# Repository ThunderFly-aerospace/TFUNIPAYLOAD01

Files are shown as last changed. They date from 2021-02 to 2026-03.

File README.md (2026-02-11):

# TFUNIPAYLOAD01 - universal interface for sensor payload 

Reference design of PX4 interface for generic [TF-ATMON](https://docs.thunderfly.cz/instruments/TF-ATMON) compatible payload. The purpose of this design is to connect a sensor to the [TF-ATMON](https://www.thunderfly.cz/tf-atmon.html) system, despite that the sensor does not have any driver in the flight stack (autopilot firmware), but at the same time, it is required for atmospheric measurement.

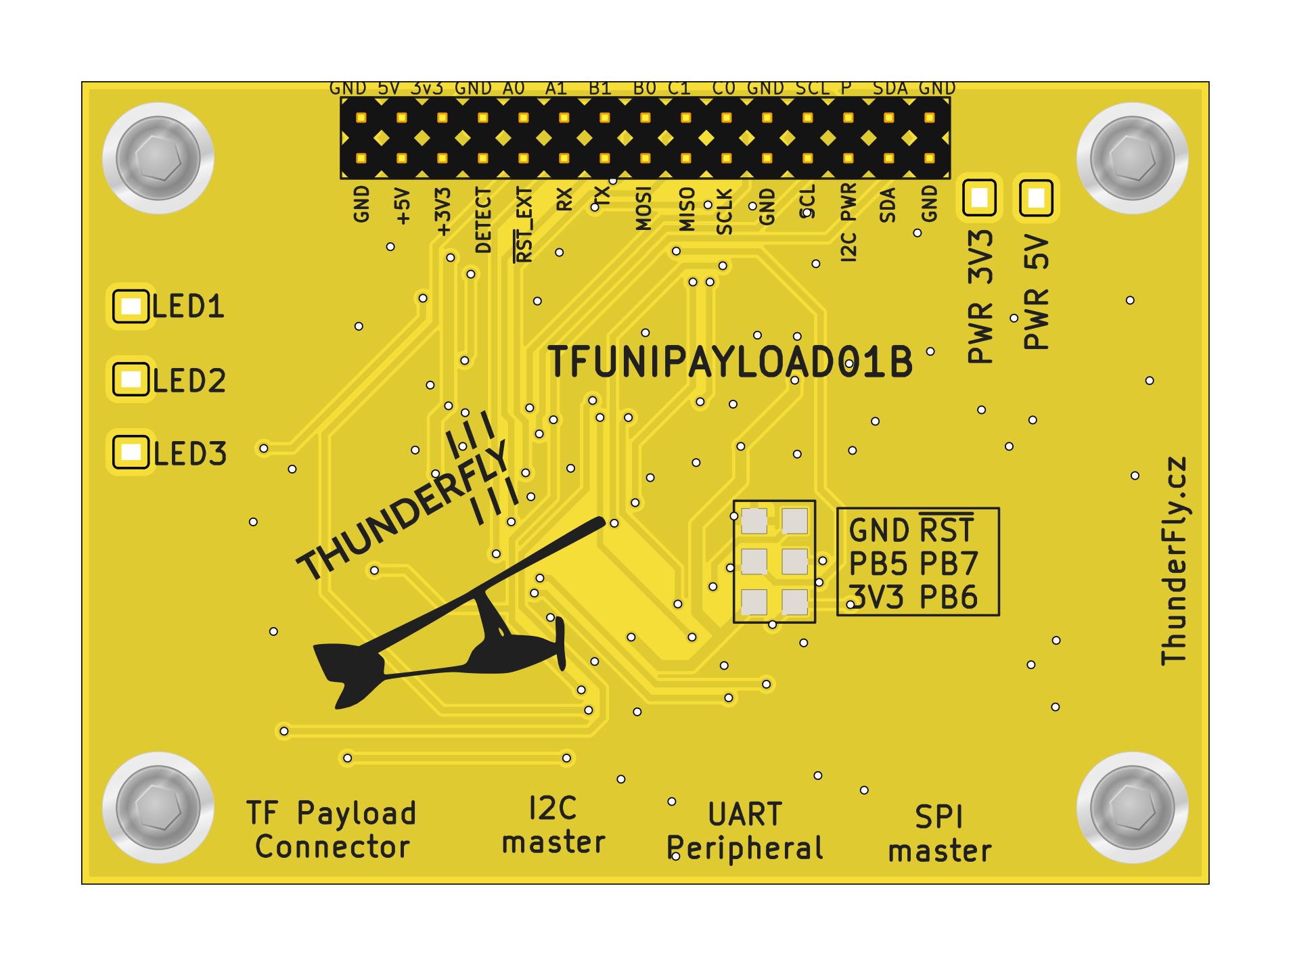
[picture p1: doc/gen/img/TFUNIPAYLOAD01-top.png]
TFUNIPAYLOAD top view


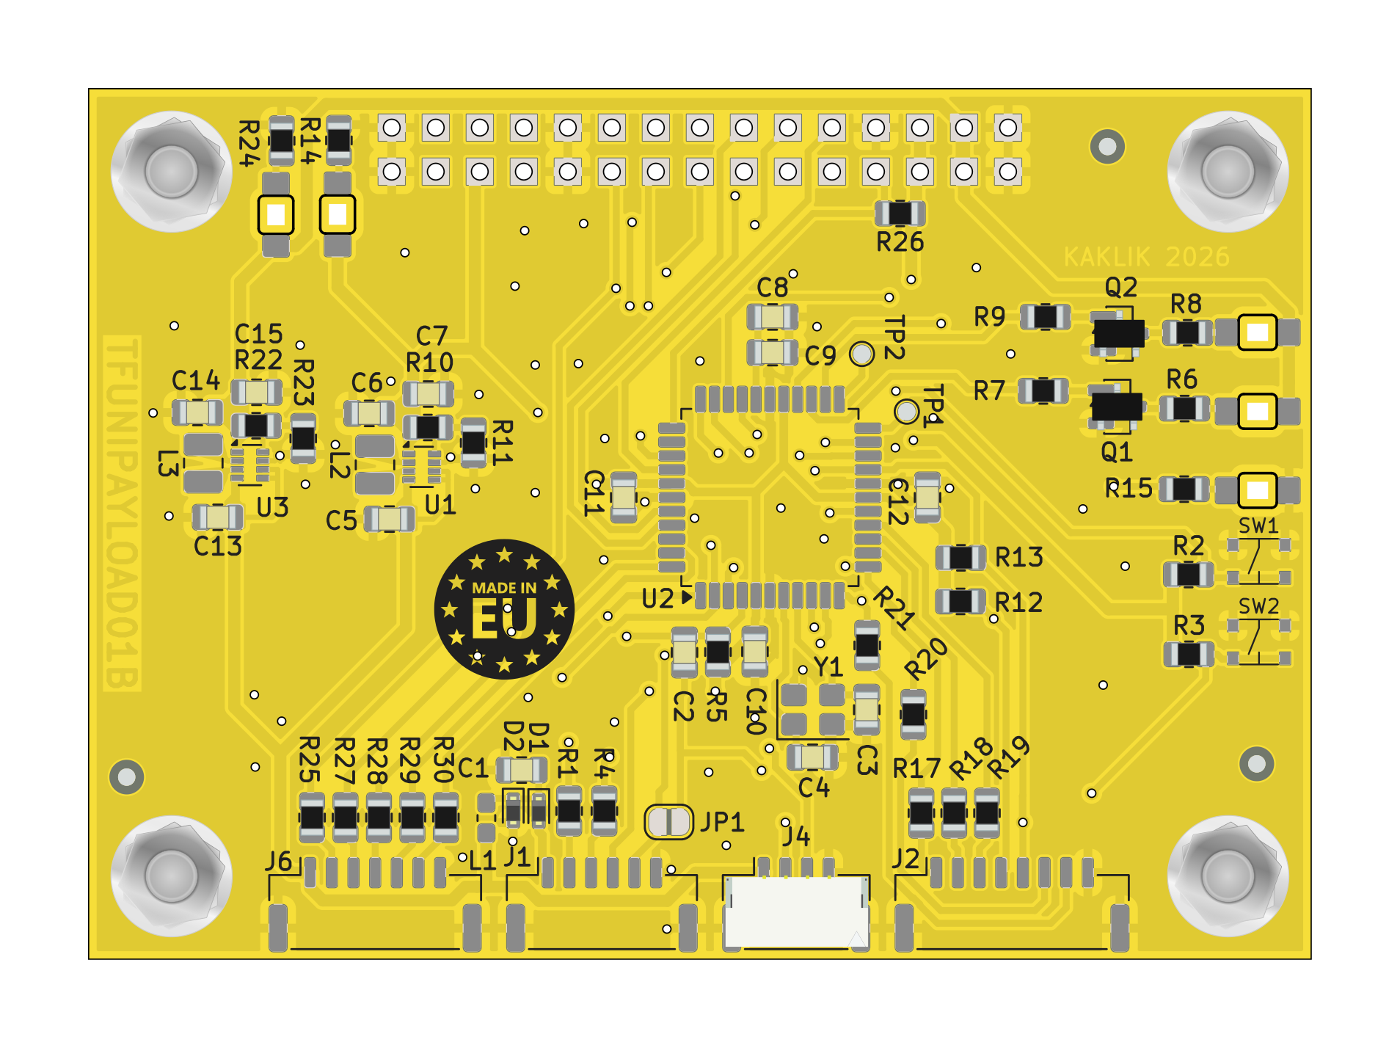
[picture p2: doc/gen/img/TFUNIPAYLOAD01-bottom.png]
TFUNIPAYLOAD01 bottom view


The sensor is connected to the TFUNIPAYLOAD board using a UART, I2C, GPIO, ADC, or SPI interface. 
ATmega in TFUNIPAYLOAD01 runs the Arduino firmware, which prepares [MAVLink](https://en.wikipedia.org/wiki/MAVLink) messages to be logged and transported to GCS running TF-ATMON infrastructure described in the block schematics. 

TFUNIPAYLOAD block-schematics

## Example of use

FMU firmware (PX4 or Ardupilot, for example) is capable of logging MAVLink data from the UART (Telemetry Port).  Therefore, the “UART Peripheral” connector on TFUNIPAYLOAD01 is intended for connecting a UART-based FMU using the Pixhawk DS-009 telemetry pinout. Typical devices include flight controllers (autopilot) or companion computers.

[Pixhawk standard connector pinout](https://github.com/pixhawk/Pixhawk-Standards/blob/master/DS-009%20Pixhawk%20Connector%20Standard.pdf) is as follows:

| Pin | Signal | Voltage levels  | Read/Write | Write |
| --- |:---:| ---:|---|---|
| 1 (red) | Vcc | +5V | Optional | Optional |
| 2 (blk) | TX (OUT)  | +3.3 V | PX4 -> Payload | -- |
| 3 (blk) | RX (IN) | +3.3 V | Payload -> PX4 | Payload -> PX4 |
| 4 (blk) | CTS (IN)  | +3.3 V | -- | -- |
| 5 (blk) | RTS (OUT) | +3.3 V | -- | -- |
| 6 (blk) | GND | GND | GND | GND |

For data to be received by the PX4 autopilot, it must have a specific form. Explicitly, it needs to use a serial link with  [MAVLink v2](https://mavlink.io/en/) packets. In that case, the [Tunnel (#385)](https://mavlink.io/en/messages/common.html#TUNNEL) packets will be stored in the autopilot's log file and forwarded to the GCS. 
The [TFUSBSERIAL01](https://github.com/ThunderFly-aerospace/TFUSBSERIAL01) hardware could be used to easily check for correct wiring. 

The following library [c_library_v2](https://github.com/mavlink/c_library_v2), which is automatically generated from message definition files, could be used. 

## Firmware examples

There are multiple Arduino-based firmware examples for different use cases. 

#### TFUNIPAYLOAD

[TFUNIPAYLOAD.ino](/SW/arduino/src/TFUNIPAYLOAD/TFUNIPAYLOAD.ino) contains a basic example, which listens to MAVLink messages from the autopilot and sends tunnel packets with random data to the autopilot.

#### TFUNIPAYLOAD_MINIMAL

Since message parsing requires a lot of memory, we have prepared an example where only [HEARTBEAT](https://mavlink.io/en/messages/common.html#HEARTBEAT) and [TUNNEL](https://mavlink.io/en/messages/common.html#TUNNEL) messages are sent. This example does not require a connected TX (from autopilot), and it is, therefore, suitable for MCUs with less memory.

Source code: [TFUNIPAYLOAD_MINIMAL.ino](/SW/arduino/src/TFUNIPAYLOAD_MINIMAL/TFUNIPAYLOAD_MINIMAL.ino)

#### Tunnel packet sending function

[Tunnel packet sending function](https://github.com/ThunderFly-aerospace/TFUNIPAYLOAD/blob/79eee22fe32725179d1df2b6ca72e901e2be1834/SW/arduino/src/TFUNIPAYLOAD/TFUNIPAYLOAD.ino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) ```  mav.SendTunnelData(data, sizeof(data), 0, 1, 0); ``` is the main function that enables sending tunnel data to the autopilot. It takes the following as its arguments:
 * data in uint8_t [127] format
 * data length
 * data type (every type of logged data will have its ID - it serves for easy differentiation of different sensors
 * target sysid
 * target compid

If the data only needs to be logged, the target sysid and compid must match the autopilot’s address, which is usually `sysid: 1, compid: 1`. If the data has to be logged and sent to GCS, broadcast must be set: `sysid: 1, compid: 0` or better `sysid: 0, compid: 0`. 

The autopilot only has a limited amount of storage memory (SD card), and it is therefore necessary to ensure, on the payload’s side, that it does not fill up during the flight. Alternatively, a maximum bandwidth on the MAVLink interface can be set in the autopilot. It is not tested what happens when the level set is exceeded[2021/09]. 

## Autopilot configuration

In the autopilot’s PX4 firmware, it is necessary to correctly set the following parameters (MAV_1_FORWARD and others will be visible only after setting the parameter MAV_1_CONFIG and rebooting the PX4): 

| Parametr | Value | Description |
|---|---|---|
| [MAV_1_CONFIG](http://docs.px4.io/main/en/advanced_config/parameter_reference.html#mavlink) | TELEM 2 | The port on which MAVLink packets will be expected. Any free TELEM port can be set |
| [MAV_1_FORWARD](http://docs.px4.io/main/en/advanced_config/parameter_reference.html#mavlink) | **1** | Enable message forwarding from this port|
| [MAV_1_RADIO_CTL](http://docs.px4.io/main/en/advanced_config/parameter_reference.html#mavlink) | **0** | |
| [MAV_1_RATE](http://docs.px4.io/main/en/advanced_config/parameter_reference.html#mavlink) | **0 B/s** | |
| [SER_TEL2_BAUD](http://docs.px4.io/main/en/advanced_config/parameter_reference.html#serial) | 57600 | It is necessary to configure the port that is set in `MAV_1_CONFIG` parameter. The setting of the baud rate port. |

How to set the parameters in PX4 is described in [manual](http://docs.px4.io/master/en/advanced_config/parameters.html#changing-a-parameter).

## How to check that the autopilot correctly receives MAVLink messages?

There are several options to find out whether the message sending is working correctly.

### Using the QGC

The message can be easily viewed live in [QGC](https://github.com/mavlink/qgroundcontrol/releases). For this procedure to function, two conditions must be fulfilled.

 1. The message must be broadcast, meaning the message must have set its target sysid and compid to 0, 0.
 2. The computer must be connected via a MAVLink instance that supports message forwarding (e.g., via TELEM1 port using modem or UART-USB converter); autopilot's USB does not support it.

 > Warning: this procedure will not work if the autopilot is connected via a USB cable to the Pixhawk's USB port.

After opening QGC, connect the autopilot to the computer (via RF modem or an external USB converter connected to the serial port). Once the autopilot is connected, live data (such as autopilot attitude) will become visible. A subsequent click on the QGC logo in the top left corner will open a menu where you select `Analyze tools` and then open `MAVLink inspector` in order to see a list of all messages. 

listener mavlin tunnel

The list of messages, when functioning correctly, should contain TUNNEL messages. 

### Using the MAVLink PX4 console

An advantage of connecting via [PX4 console](https://docs.px4.io/main/en/debug/consoles.html) lies in its independence from broadcasting settings and the possibility of checking whether the message is received and parsed by the autopilot. If the message is visible here (and the logging is enabled), it is at the same time already logged. With this procedure, a USB cable connection to the autopilot can be used. 

Autopilot console can be entered using the following Python [script](https://github.com/ThunderFly-aerospace/PX4Firmware/blob/master/Tools/mavlink_shell.py) or using [QGC](https://github.com/mavlink/qgroundcontrol/releases).

 * In the case of using a Python script, it is enough to run the python3 script with a parameter of the chosen serial link to which the autopilot/modem is connected.
 * In the case of using QGC, the QGC must be opened in the autopilot console by clicking on the QGC logo (on the top), choosing `Analyze tools`, and choosing a console.

The received message can then be retrieved using the following command:

`listener mavlink_tunnel`

The command displays the current tunnel message. Adding the -n 100` parameter will cause a listing of 100 messages (and the new message will display by itself).

If the communication is working properly, the output should look like this:

mavlink tunnel uorb message

### From a uLog file

The tunnel message can be logged into autopilot in a standard [uLog format](https://docs.px4.io/main/en/dev_log/ulog_file_format.html). However, because tools like [Flight review](https://review.px4.io/) are unable to display such data format, it is necessary to overcome this problem using a suitable tool. One option is using the [PlotJuggler](https://plotjuggler.io/). 
Another possibility for opening the log is the [Jupiter notebook](https://github.com/ThunderFly-aerospace/TFUNIPAYLOAD/blob/master/SW/LogViewer/ReadTunnelData.ipynb).

## Known limitations

  * Avoiding overloading the autopilot's memory with messages must be ensured on the payload side
  * A maximum of 2 devices + modem or 3 devices without a modem can be connected in this way. The limitation is caused by the MAVLink driver, which is only able to connect a maximum of 3 instances of MAVLink devices, and also due to the limited number of UART interfaces of the autopilot.
  * It is not possible for the input of payload messages and output to [sik modem](https://github.com/ThunderFly-aerospace/TFSIK01) to have the same type of MAVLink messages (stream) that would differ only in the number of messages per second. This means that it is not possible to simply select a data stream to be transmitted to the ground from the data stream intended for logging. If it is necessary to log more detailed data (with higher frequency) another MAVLink message must be logged.

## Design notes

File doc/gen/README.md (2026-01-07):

# PCB

Board size: 70.61x50.29 mm (2.78x1.98 inches)

- This is the size of the rectangle that contains the board
- Thickness: 1.66 mm (65 mils)
- Material: FR4
- Finish: HAL lead-free
- Layers: 2
- Copper thickness: 35 µm

Solder mask: TOP / BOTTOM

- Color: Green

Silk screen: TOP / BOTTOM

- Color: White

Stackup:

| Name | Type | Color | Thickness [µm]| Material | Er | Loss tan |
|---|---|---|---|---|---|---|
| F.SilkS | Top Silk Screen | | | | | |
| F.Paste | Top Solder Paste | | | | | |
| F.Mask | Top Solder Mask | | 10 | | | |
| F.Cu | copper | | 35 | | | |
| dielectric 1 | core | | 1570 | FR4 | 4.5 | 0.020 |
| B.Cu | copper | | 35 | | | |
| B.Mask | Bottom Solder Mask | | 10 | | | |
| B.Paste | Bottom Solder Paste  | | | | | |
| B.SilkS | Bottom Silk Screen | | | | | |

# Important sizes

Clearance: 0.2 mm (8 mils)

Track width: 0.3 mm (12 mils)

- By design rules: 0.2 mm (8 mils)

Drill: 0.5 mm (20 mils)

- Vias: 0.5 mm (20 mils) [Design: 0.4 mm (16 mils)]
- Pads: 1.0 mm (39 mils)
- The above values are real drill sizes, they add 0.1 mm (4 mils) to plated holes (PTH)

Via: 0.8/0.4 mm (31/16 mils)

- By design rules: 0.8/0.3 mm (31/12 mils)
- Micro via: yes [0.2/0.1 mm (8/4 mils)]
- Buried/blind via: yes
- Total: 96 (thru: 96 buried/blind: 0 micro: 0)

Outer Annular Ring: 0.15 mm (6 mils)

- By design rules: 0.26 mm (10 mils)

Eurocircuits class: 4B
- Using min drill 0.5 mm for an OAR of 0.15 mm

# General stats

Components count: (SMD/THT)

- Top: 1/6 (SMD + THT)
- Bottom: 69/0 (SMD)

Defined tracks:

- 0.25 mm (10 mils)
- 0.3 mm (12 mils)
- 0.4 mm (16 mils)
- 0.5 mm (20 mils)
- 0.6 mm (24 mils)
- 0.7 mm (28 mils)
- 0.8 mm (31 mils)

Used tracks:

- 0.3 mm (12 mils) (37) defined: yes
- 0.4 mm (16 mils) (477) defined: yes
- 0.5 mm (20 mils) (22) defined: yes
- 0.7 mm (28 mils) (102) defined: yes

Defined vias:

Used vias:

- 0.8/0.4 mm (31/16 mils) (Count: 96, Aspect: 2.1 A) defined: no

Holes (excluding vias):

- 0.89 mm (35 mils) (30)
- 3.0 mm (118 mils) (4)

Oval holes:

Drill tools (including vias and computing adjusts and rounding):

- 0.5 mm (20 mils) (96)
- 1.0 mm (39 mils) (30)
- 3.1 mm (122 mils) (4)

Solder paste stats:

Using a paste with 87.75 % alloy, that has an specific gravity for the alloy of 7.4 g/cm³
and 1.0 g/cm³ for the flux. This paste has an specific gravity of  4.15 g/cm³.

The stencil thickness is  0.12 mm.

| Side | Pads with paste | Area [mm²] | Paste [g] |
|---|---|---|---|
| Total  | 219 | 253.53 | 1.26 |

Note: this is just an approximation to the theoretical value. Margins of the solder mask and waste aren't computed.

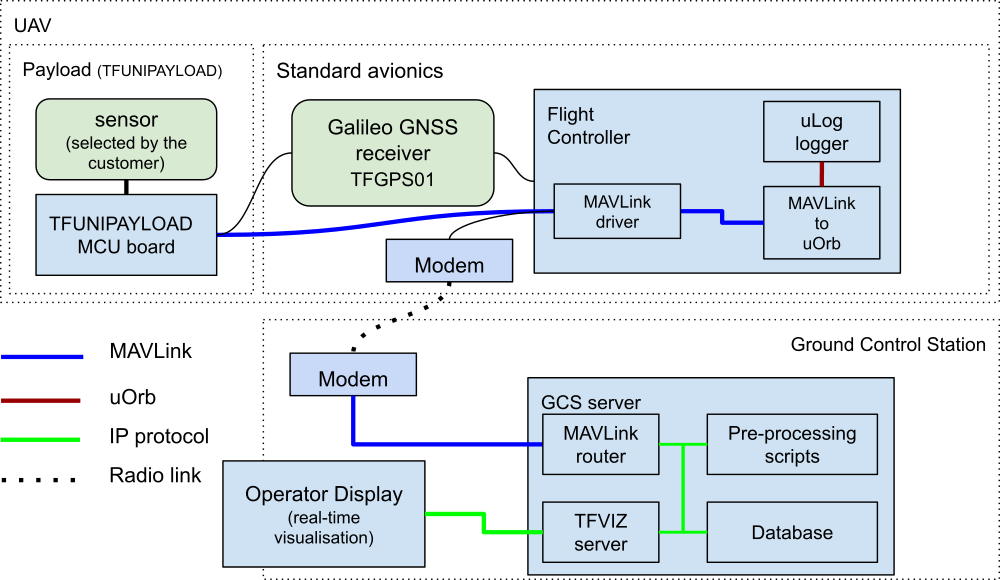
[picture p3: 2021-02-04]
doc/img/block_schematics.png

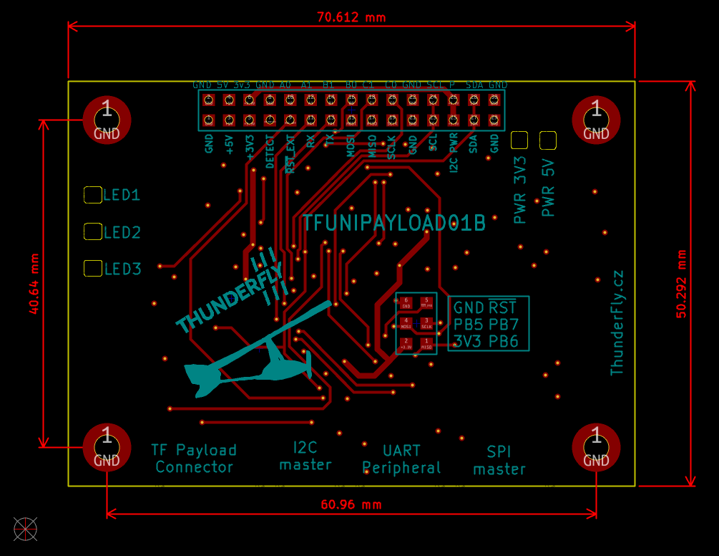
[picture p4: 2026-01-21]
doc/img/TFUNIPAYLOAD01_dimensions.png

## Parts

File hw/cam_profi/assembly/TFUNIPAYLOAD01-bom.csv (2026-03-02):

Component | Description | Part | References | Value | Footprint | Quantity Per PCB | Datasheet | ust_id | sim.device | sim.pins | height | mouser part number | mouser price/stock | manufacturer_name | manufacturer_part_number
1 | Unpolarized capacitor, small symbol | C_Small | C3C4 | 15p | C_0805_2012Metric | 2 | ~ | 5c70984712875079b91f8b32
2 | Unpolarized capacitor | C | C9C10C11C12 | 100nF | C_0805_2012Metric | 4 | ~ | 6508260b462c6d9e720541f1 5c70984712875079b91f8b4c
3 | Unpolarized capacitor | C | C2 | 4u7 | C_0805_2012Metric | 1 | ~ | 5e3ff8fc1287502a33bad7a3
4 | Unpolarized capacitor | C | C1C7C8C15 | 10uF | C_0805_2012Metric | 4 | ~ | 5c70984712875079b91f8b53
5 | Unpolarized capacitor, small symbol | C_Small | C5C13 | 22u | C_0805_2012Metric | 2 | ~ | 650b58f1462c6d9e7205463b
6 | Unpolarized capacitor, small symbol | C_Small | C6C14 | 47u | C_0805_2012Metric | 2 | ~ | 5c70984812875079b91f8bbf
7 | 100V, 0.25A, High-speed Switching Diode, SOD-523 | BAS516 | D1 | BAS516 | D_SOD-523 | 1 | https://assets.nexperia.com/documents/data-sheet/BAS16_SER.pdf | 693421c6ea235ce78ba25972 | D | 1=K 2=A
8 | Light emitting diode | LED | D3 | BLUE | LED_1206_mill | 1 | https://v4.cecdn.yun300.cn/100001_2003185297/17%20FYLS-1206XXXC-D.pdf | 5c70984512875079b91f8898
9 | Zener diode | D_Zener | D2 | BZX585-B5V6.115 | D_SOD-523 | 1 | https://www.tme.eu/Document/7f59fc987b8fce7e4ab18399d6e66bd1/BZX585-DTE.pdf | 60879d38128750769ee58e48
10 | Light emitting diode | LED | D6 | GREEN | LED_1206_mill | 1 | ~ | 5c70984412875079b91f8895
11 | Light emitting diode | LED | D4D5D7 | RED | LED_1206_mill | 3 | ~ | 5c70984412875079b91f8896
12 | 2x15 2.54 mm pitch header | HEADER_2x15 | J5 | HEADER_2x15 | Straight_2x15 | 1 |  | 68226dbfee7fc534862c67d1
13 |  | SM04B-GHS-TB | J4 | SM04B-GHS-TB | JST_GH_SM04B-GHS-TB_1x04-1MP_P1.25mm_Horizontal | 1 |  | 5c86273d1287500b4e0280be
14 | 1x07 2.54 mm pitch header | SM06B-GHS-TB | J1 | SM06B-GHS-TB | JST_GH_SM06B-GHS-TB_1x06-1MP_P1.25mm_Horizontal | 1 |  | 5fa0f70212875025b3977932
15 | 1x08 2.54 mm pitch header | SM07B-GHS-TB | J6 | SM07B-GHS-TB | JST_GH_SM07B-GHS-TB_1x07-1MP_P1.25mm_Horizontal | 1 |  | 5c7250081287500b4e112e78
16 | 1x08 2.54 mm pitch header | SM08B-GHS-TB | J2 | SM08B-GHS-TB | JST_GH_SM08B-GHS-TB_1x08-1MP_P1.25mm_Horizontal | 1 |  | 5fa0f75012875025b3977948
17 | Inductor | L | L2L3 | 1uH - DFE252012P-1R0M=P2 | L_1008_2520Metric | 2 | ~ | 650b5977462c6d9e72054656
18 | Inductor with ferrite core, small symbol | L_Ferrite_Small | L1 | NL03KT330 | L_0603_1608Metric_Pad1.05x0.95mm_HandSolder | 1 | ~ | 64fe1808f3b9d36f37fc944d
19 | 0.8A Ic, 45V Vce, NPN Transistor, SOT-23 | BC817 | Q1Q2 | BC817-25 | SOT-23 | 2 | ~ | 5c70984712875079b91f8aea
20 | Resistor | R | R1R4R6R15R17R18R19R20R21R25R27R28R29R30 | 100R | R_0805_2012Metric | 14 | ~ | 5c70984512875079b91f8977 5c70984512875079b91f8956
21 | Resistor | R | R8R14R24 | 180R | R_0805_2012Metric | 3 | ~ | 5c70984512875079b91f897c
22 | Resistor, small symbol | R_Small | R2R3R5R7R9R12R13R26 | 10k | R_0805_2012Metric | 8 | ~ | 5c70984612875079b91f899f 5c70984512875079b91f8962
23 | Resistor, small symbol | R_Small | R11R23 | 91k | R_0805_2012Metric | 2 | ~ | 5c70984712875079b91f8a95
24 | Resistor, small symbol | R_Small | R10 | 511k | R_0805_2012Metric | 1 | ~ | 650b5a43462c6d9e7205468e
25 | Resistor, small symbol | R_Small | R22 | 806k | R_0805_2012Metric | 1 | ~ | 650b5abb462c6d9e720546b8
26 | Push button switch, generic, two pins | SW_Push | SW1SW2 | SKRTLAE010 | KMT031 NGJ LHS C&K | 2 | ~ | 612515a61287500165a9771d
27 | 20MHz, 128kB Flash, 16kB SRAM, 4kB EEPROM, JTAG, TQFP-44 | ATmega1284P-A | U2 | ATMEGA1284P-AU | TQFP-44_10x10mm_P0.8mm | 1 | http://www.atmel.com/Images/Atmel-8272-8-bit-AVR-microcontroller-ATmega164A_PA-324A_PA-644A_PA-1284_P_datasheet.pdf | 5c70984412875079b91f888e
28 | Switching Voltage Regulators 1.5-A output current, high power density buck-boost converter | TPS631000DRLR | U1U3 | TPS631000DRLR | SOT-583-8 | 2 | https://www.ti.com/lit/ds/symlink/tps631000.pdf?ts=1652152702265 | 63de5ae4ae0b2d5aa05e2714 |  |  | 0.5 | 595-TPS631000DRLR | https://www.mouser.co.uk/ProductDetail/Texas-Instruments/TPS631000DRLR?qs=rSMjJ%252B1ewcRYwoN2deTeNA%3D%3D | Texas Instruments | TPS631000DRLR
29 | Four pin crystal, GND on pins 2 and 4, small symbol | Crystal_GND24_Small | Y1 | 8 MHz | Crystal_SMD_3225-4Pin_3.2x2.5mm | 1 | ~ | 65481c4c462c6d9e72056ac8

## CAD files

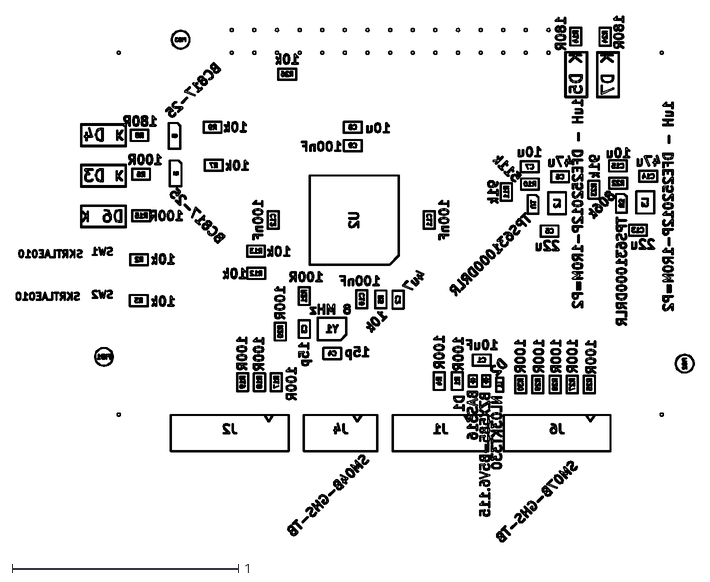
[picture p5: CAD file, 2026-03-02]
doc/gen/dxf/TFUNIPAYLOAD01-B_Fab.dxf
3.00 x 2.32

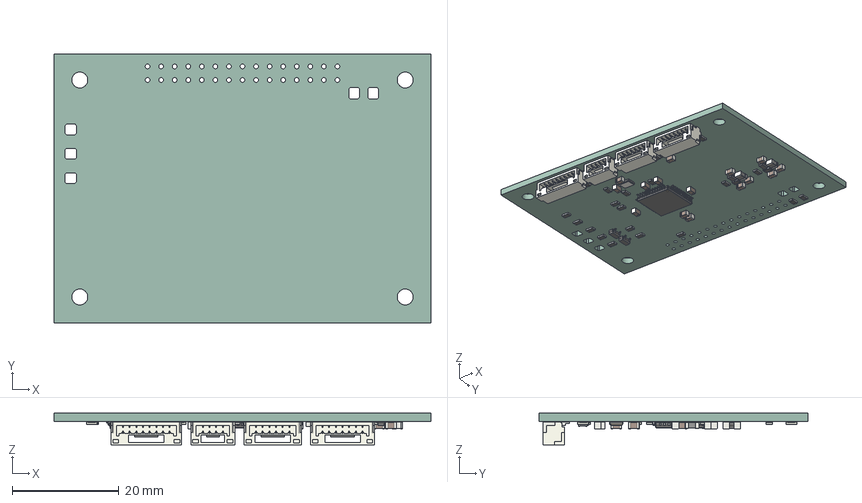
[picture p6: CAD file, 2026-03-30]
doc/gen/TFUNIPAYLOAD01.step
70.6 x 50.3 x 5.90 mm
C_0805_2012Metric x 15
TQFP-44_10x10mm_P0.8mm
R_0805_2012Metric x 29
SOT-583-8 x 2
JST_GH_SM06B-GHS-TB_1x06-1MP_P1.25mm_Horizontal
SOT-23 x 2
L_0603_1608Metric
JST_GH_SM08B-GHS-TB_1x08-1MP_P1.25mm_Horizontal
JST_GH_SM07B-GHS-TB_1x07-1MP_P1.25mm_Horizontal
JST_GH_SM04B-GHS-TB_1x04-1MP_P1.25mm_Horizontal
D_SOD-523 x 2
Crystal_SMD_3225-4Pin_3.2x2.5mm
L_1008_2520Metric x 2
kibot_iueybrui_PCB

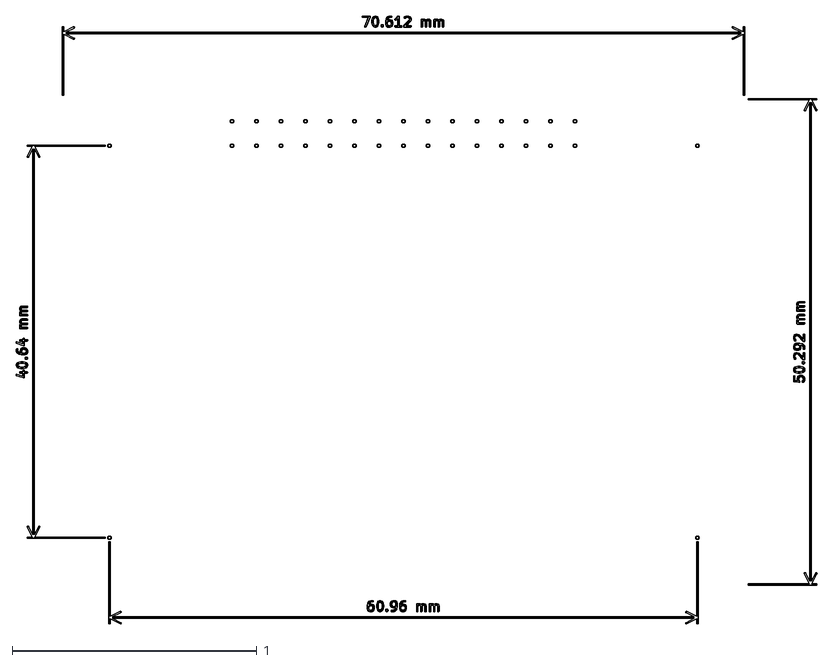
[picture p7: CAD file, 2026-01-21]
doc/gen/dxf/TFUNIPAYLOAD01-User_Comments.dxf
3.27 x 2.48

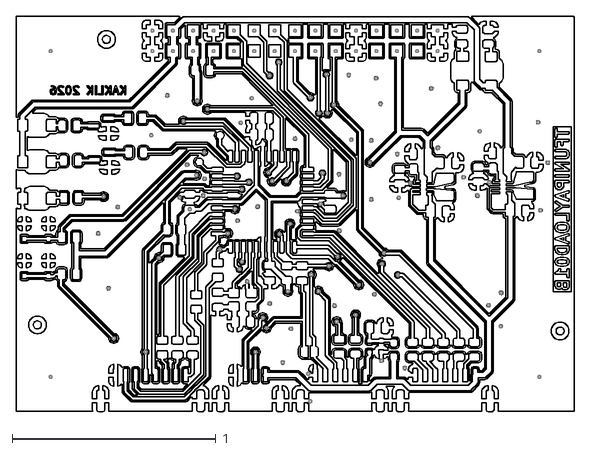
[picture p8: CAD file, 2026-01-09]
doc/gen/dxf/TFUNIPAYLOAD01-B_Cu.dxf
2.74 x 1.94

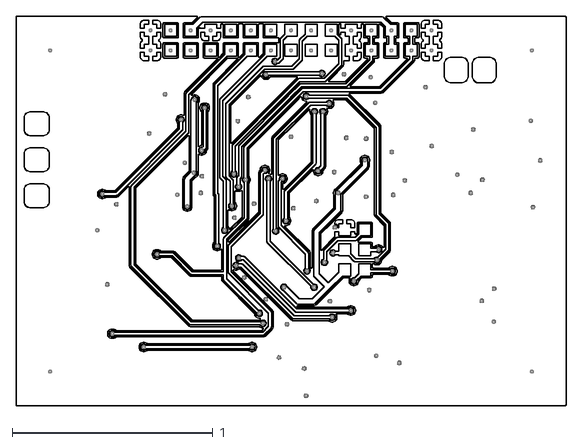
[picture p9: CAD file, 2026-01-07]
doc/gen/dxf/TFUNIPAYLOAD01-F_Cu.dxf
2.74 x 1.94

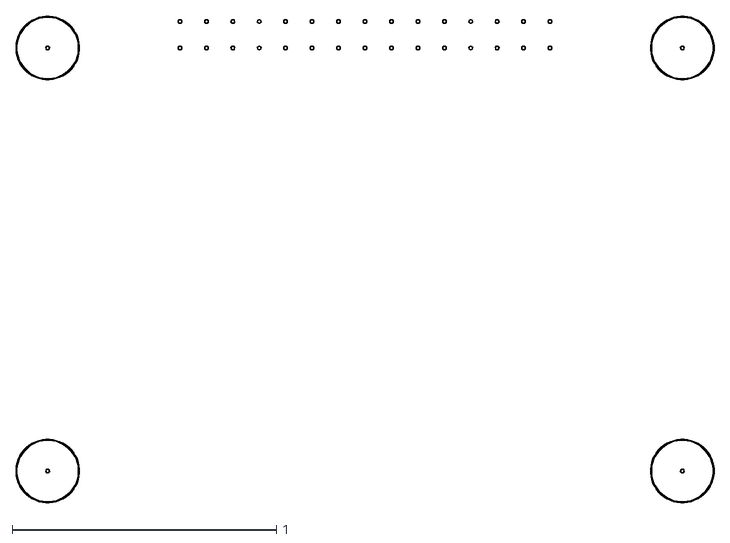
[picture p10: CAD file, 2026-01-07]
doc/gen/dxf/TFUNIPAYLOAD01-F_Fab.dxf
2.64 x 1.84

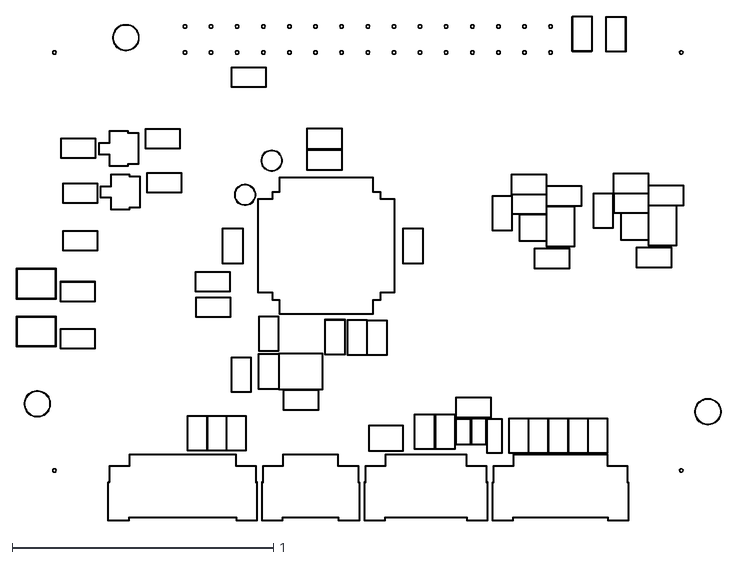
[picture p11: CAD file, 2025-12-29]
doc/gen/dxf/TFUNIPAYLOAD01-B_Courtyard.dxf
2.70 x 1.93

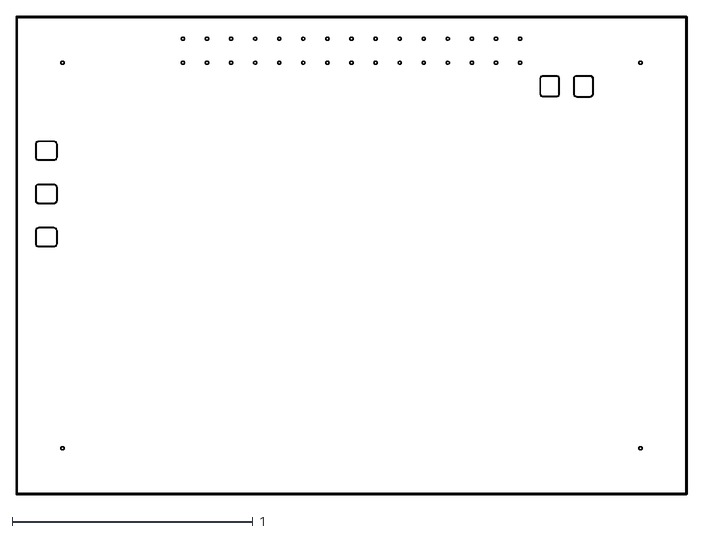
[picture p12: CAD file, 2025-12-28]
doc/gen/dxf/TFUNIPAYLOAD01-Edge_Cuts.dxf
2.79 x 1.99

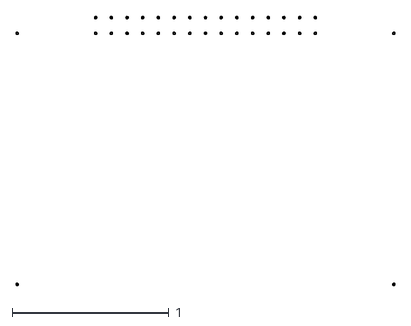
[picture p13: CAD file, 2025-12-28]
doc/gen/dxf/TFUNIPAYLOAD01-User_Drawings.dxf
2.41 x 1.71

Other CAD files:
doc/gen/dxf/TFUNIPAYLOAD01-B_Mask.dxf
doc/gen/dxf/TFUNIPAYLOAD01-B_Paste.dxf
doc/gen/dxf/TFUNIPAYLOAD01-B_Silkscreen.dxf
doc/gen/dxf/TFUNIPAYLOAD01-F_Mask.dxf
doc/gen/dxf/TFUNIPAYLOAD01-F_Paste.dxf
doc/gen/dxf/TFUNIPAYLOAD01-F_Silkscreen.dxf

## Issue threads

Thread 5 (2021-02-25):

Základní snímače - pomocné měření

kaklik, 2021-02-25:
Je pravděpodobné, že pro většinu měření bude potřebné snímat některé pomocné atmosférické veličiny. Napadá mě:

- Tlak vzduchu (aktuálně měřeno uvnitř autopilota)
- Teplota vzduchu (Nějak měří autopilot, nepřímo, teplotou různých jiných čidel, IMU, barometr a podobně)
- Relativní vlhkost  - aktuálně není měřeno vůbec.

Tyto parametry budou potřeba pro jiná měřění jako:

- Měření ionizujícího záření #4
- Měření elektrického pole
- Měření koncentrace iontů

## Měření relativní vlhkosti a teploty

Měření těchto dvou veličin je poměrně provázané protože relativní vlhkost se přímo mění s teplotou. Dále je to čidlo, které je velmi běžně rozšířené.
V našem případě by asi bylo vhodné použít [sht31](https://www.sensirion.com/en/environmental-sensors/humidity-sensors/digital-humidity-sensors-for-various-applications/), [SHT40](https://www.soselectronic.cz/articles/sensirion/senzor-vlhkosti-a-teploty-sht40-2527), [SHT40](https://www.soselectronic.cz/products/sensirion/sht40-ad1b-r2-343550)
Vzniká tak otázka zda se tohle čidlo snažit zabudovat do TFUNIPAYLOAD, nebo spíše postupovat tak, že bychom měli separátní PCB, optimalizované pro přímé připojení do autopilota. S tím, že v autopilotovi by byl driver pro čtení přímo takového snímače.

Například podle [tohoto článku](https://www.mdpi.com/1424-8220/20/23/6819) relativní vlhkost často interferuje s měřením koncentrace pevných částic. Většina snímačů pevných částic dává relevantní hodnoty pouze při relativní vlhkosti menší než 85%.

### Výhody:

- Čidlo by šlo použít i mimo TFATMON měření
- Měření může být přímo logováno autopilotem jako separátní zpráva měřená asynchronně s měřením z TFUNIPAYLOAD.
- Mohlo by to být základní "demoaplikací", na které by si zákazníci snadno vyzkoušeli náš systém, v podsatě něco jako reklamní produkt.

### Nevýhody:

- Zákazník by teoreticky mohl částečně obejít náš systém a nepotřebovat ho v případě, že by mu tohle čidlo stačilo ke spokojenosti.
- Měření bude asynchronní k TFUNIPAYLOAD měřením, na druhou stranu je tohle spíš teoretické omezení. Protože jednak reakční doba samotného snímače je poměrně pomalá a potom lze situaci vyřešít tím, že se bude logovat několikrát za sekundu v autopilotovi
- Data ze senzoru nebudou do pozemní stanice posílána jako pro TF-ATMON standardní tunnel packety. Znamená to, pozemní stanici TF-ATMON naučit pracovat i s jinými telemetrickými daty z autopilota.

kaklik, 2022-11-12:
Tohle je v [PX4 nyní již implementované](https://github.com/PX4/PX4-Autopilot/tree/main/src/drivers/hygrometer). Chybí ale [návod k driveru](https://docs.px4.io/main/en/modules/modules_driver_airspeed_sensor.html).

kaklik, 2023-04-21:
Tohle issue mi připadá, že je vyřešeno použitím [TFHT01](https://www.tindie.com/products/thunderfly/tfht01-aerial-hygrometer-and-thermometer/). Maximálně lze vylepšit jeho dokumentaci a příklady použití, což je nad rámec tohoto zadání.

Closed 2023-04-21.

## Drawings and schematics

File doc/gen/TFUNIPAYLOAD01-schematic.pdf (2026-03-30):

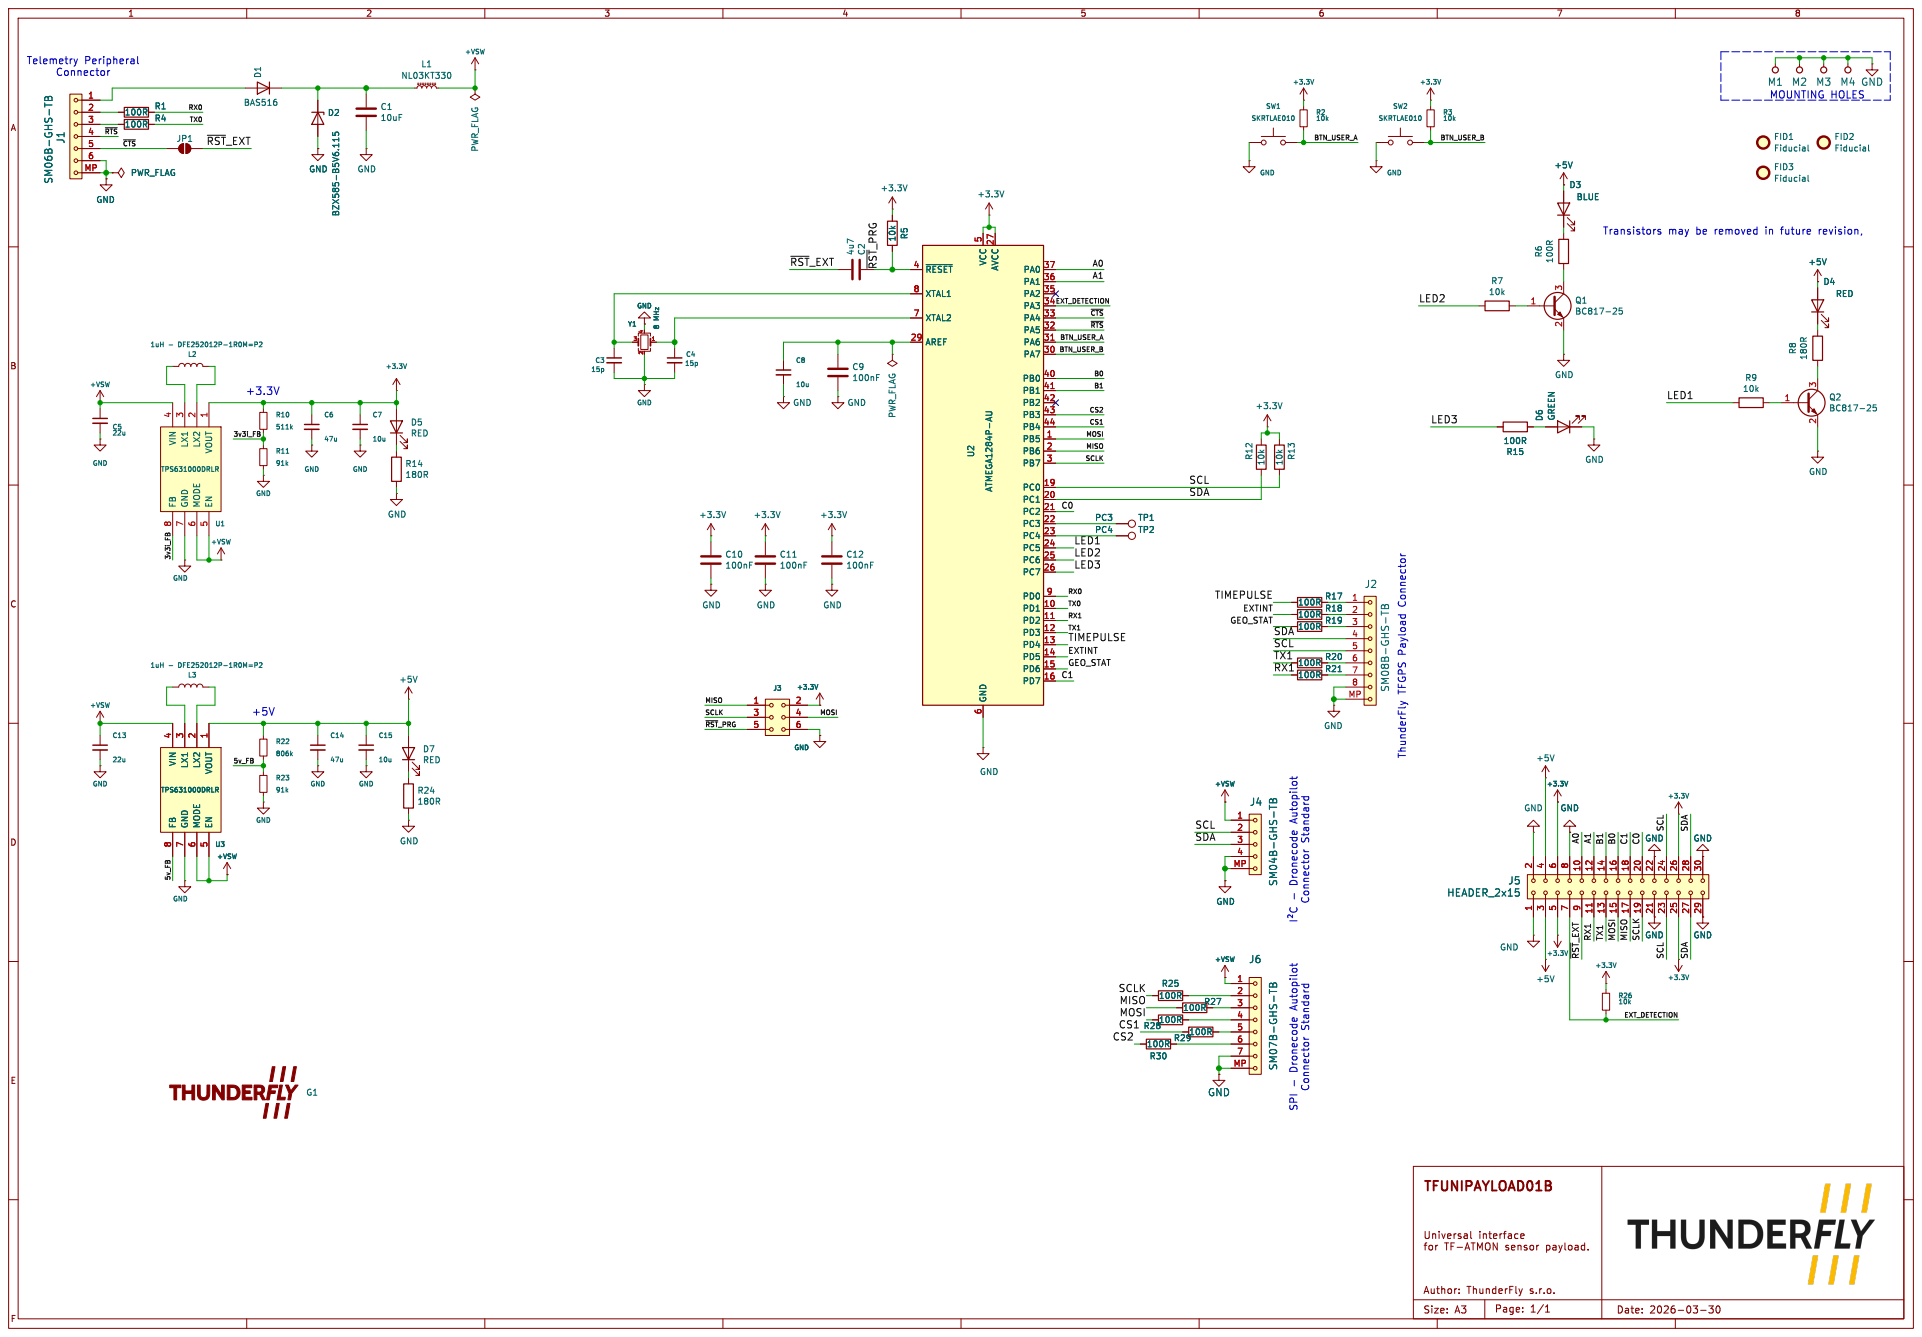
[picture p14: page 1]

MOUNTING HOLES ThunderFly TFGPS Payload Connector

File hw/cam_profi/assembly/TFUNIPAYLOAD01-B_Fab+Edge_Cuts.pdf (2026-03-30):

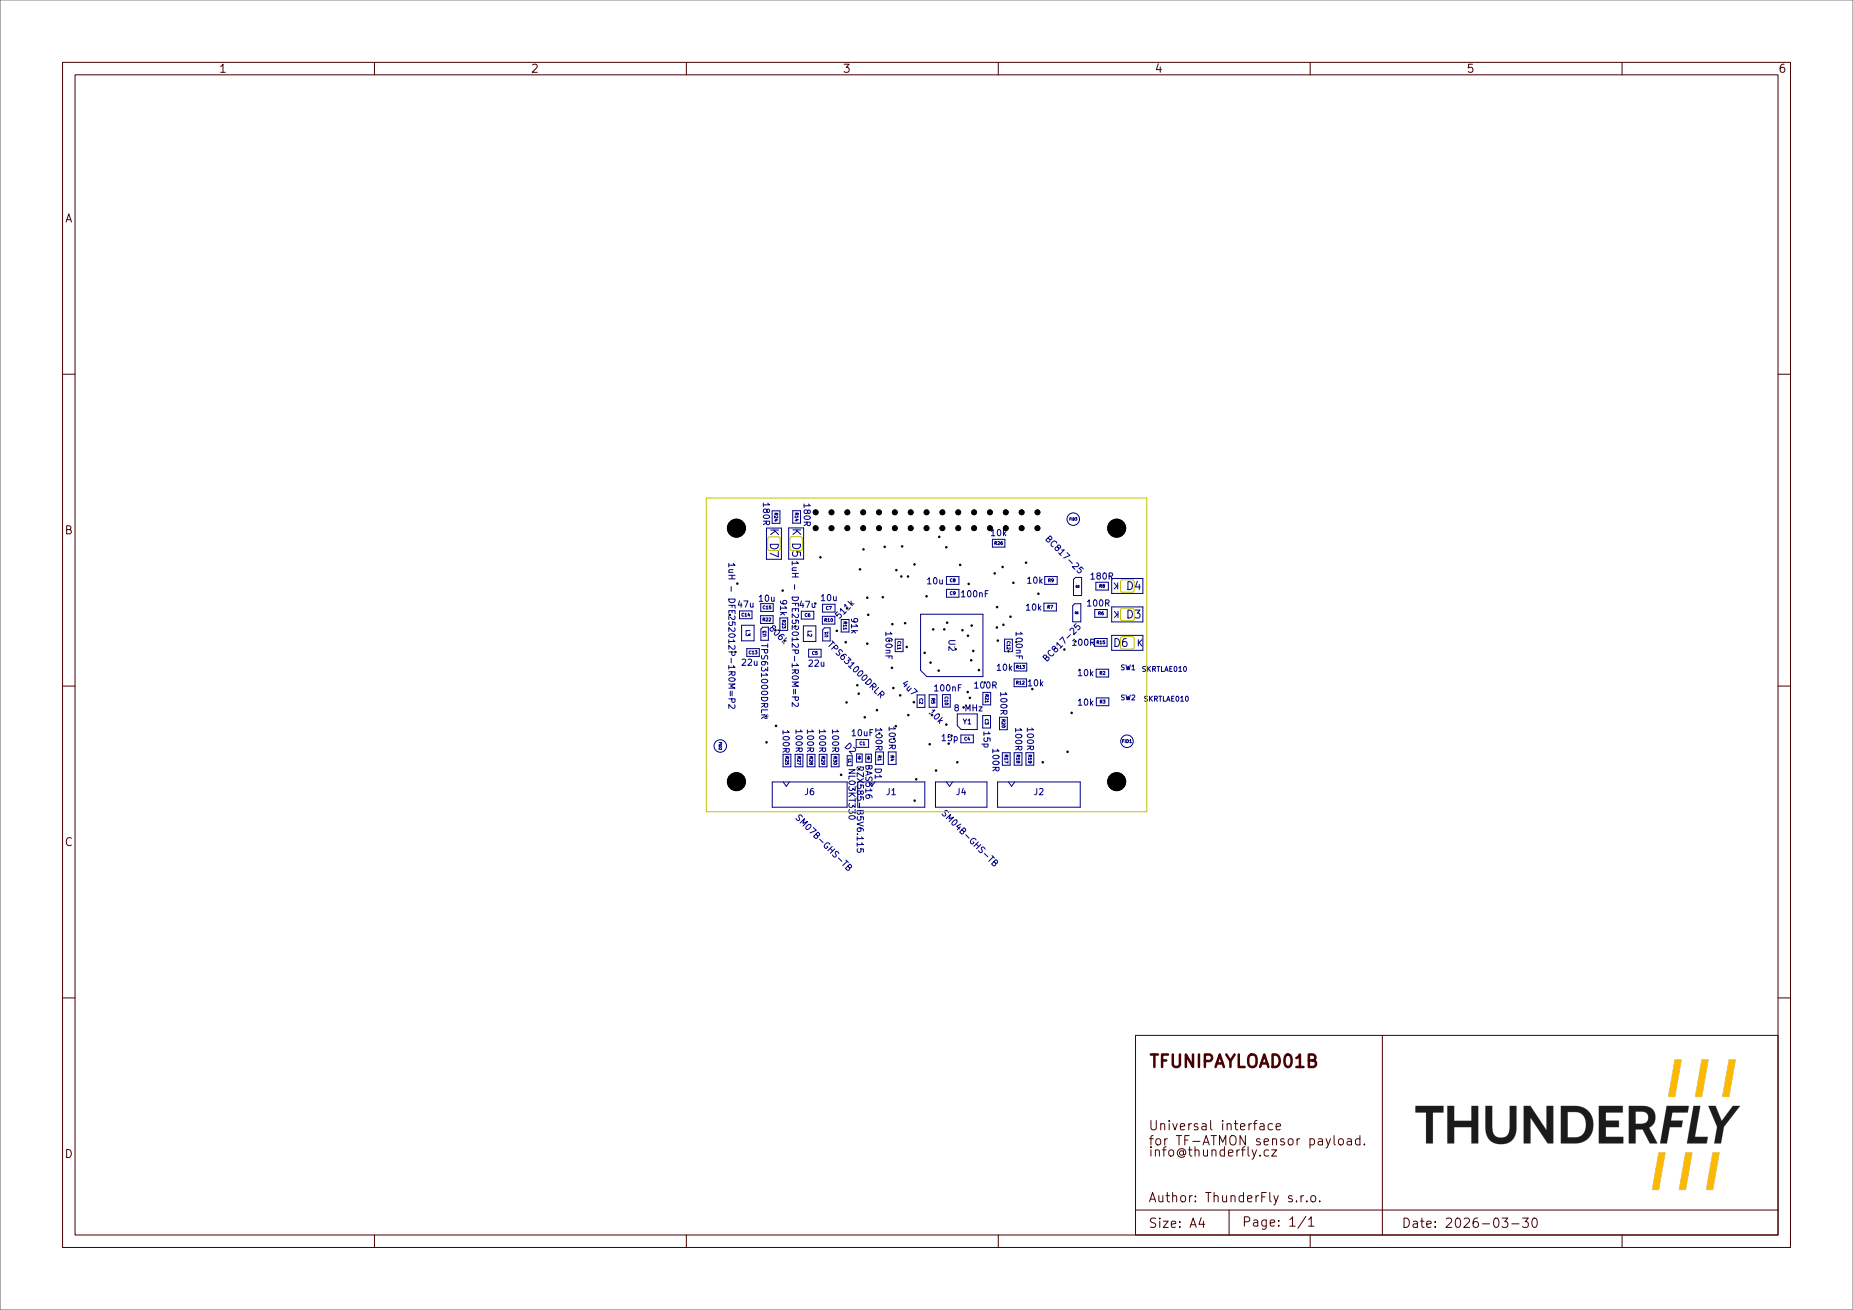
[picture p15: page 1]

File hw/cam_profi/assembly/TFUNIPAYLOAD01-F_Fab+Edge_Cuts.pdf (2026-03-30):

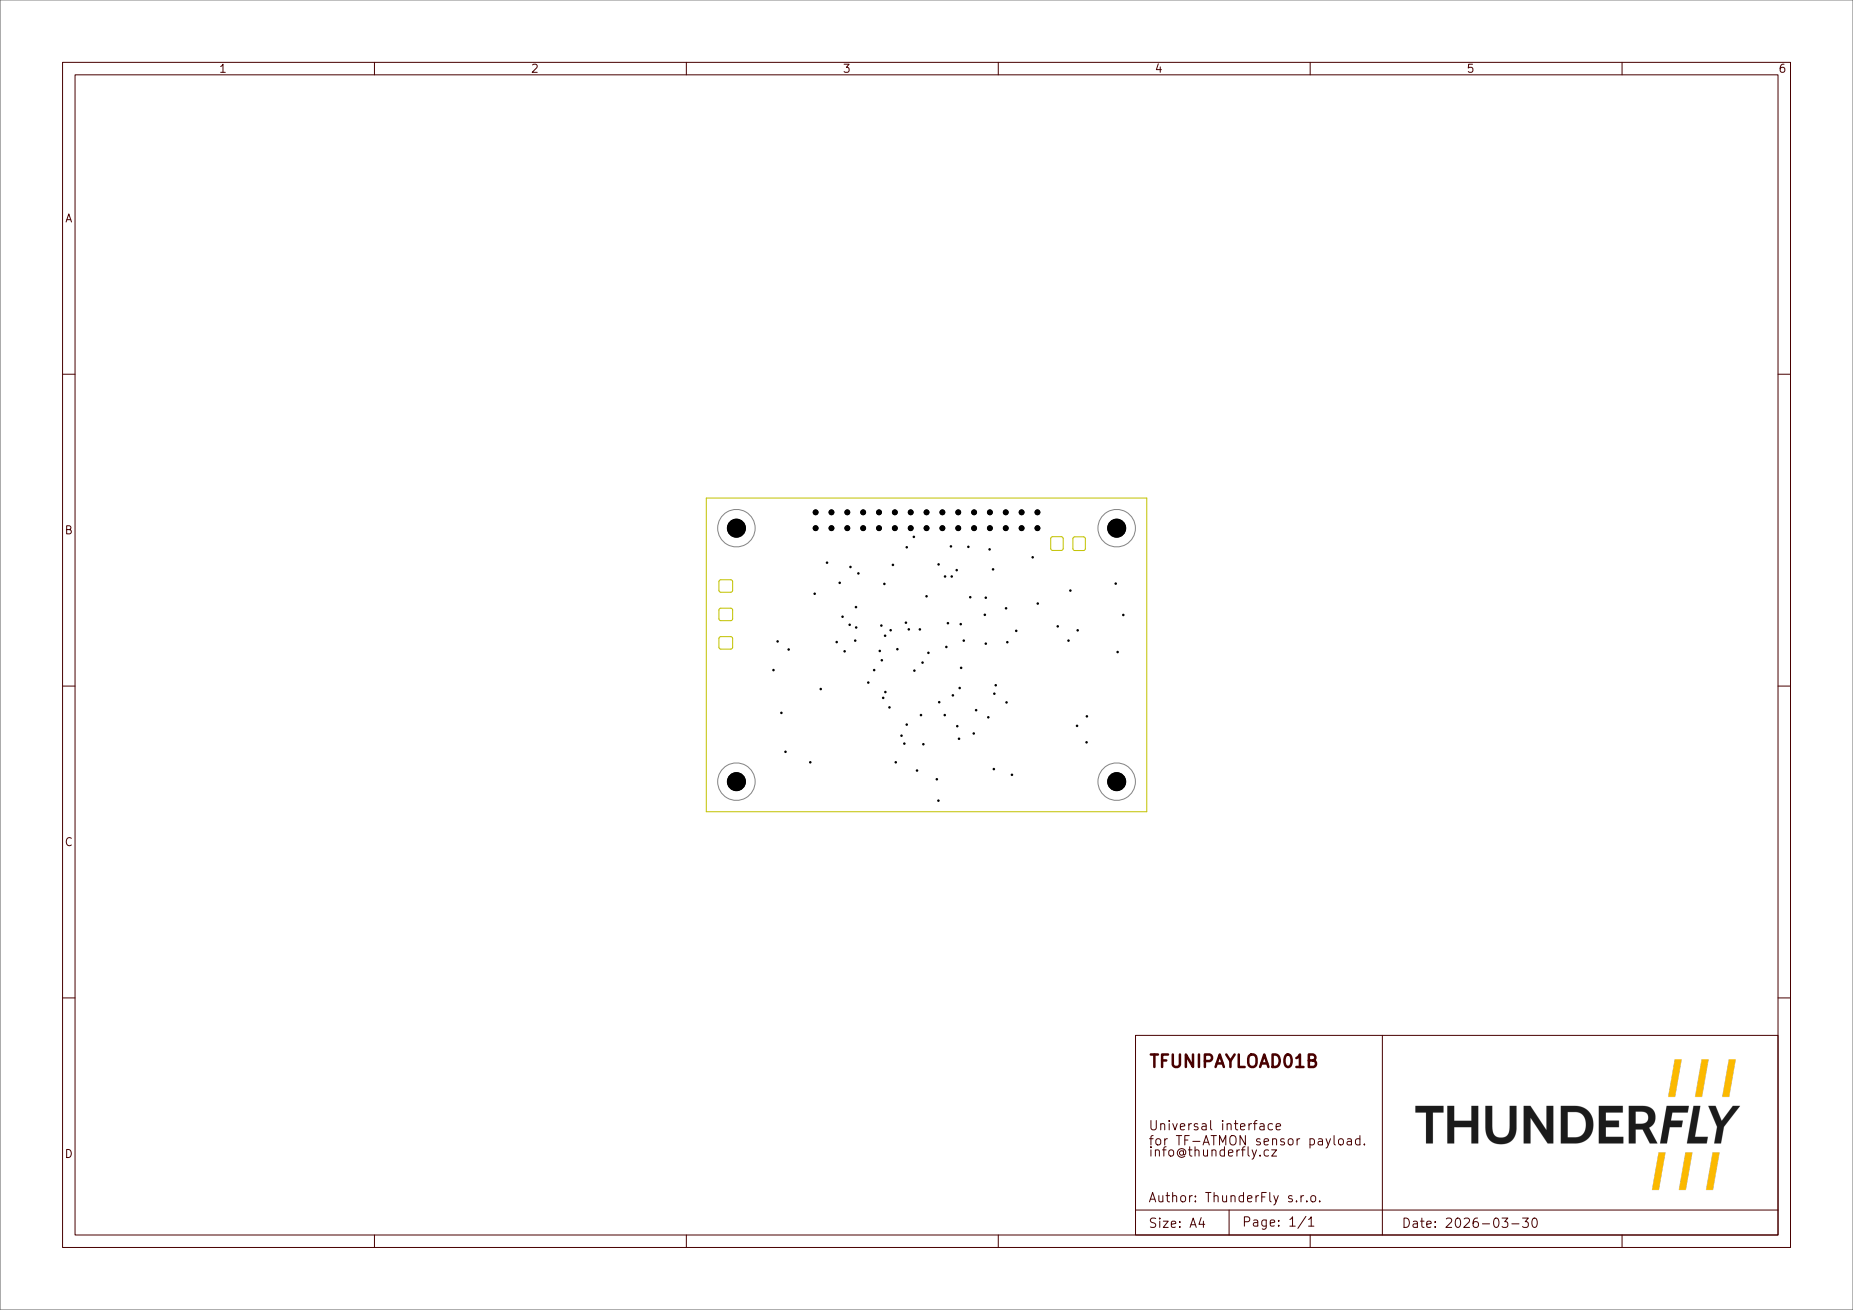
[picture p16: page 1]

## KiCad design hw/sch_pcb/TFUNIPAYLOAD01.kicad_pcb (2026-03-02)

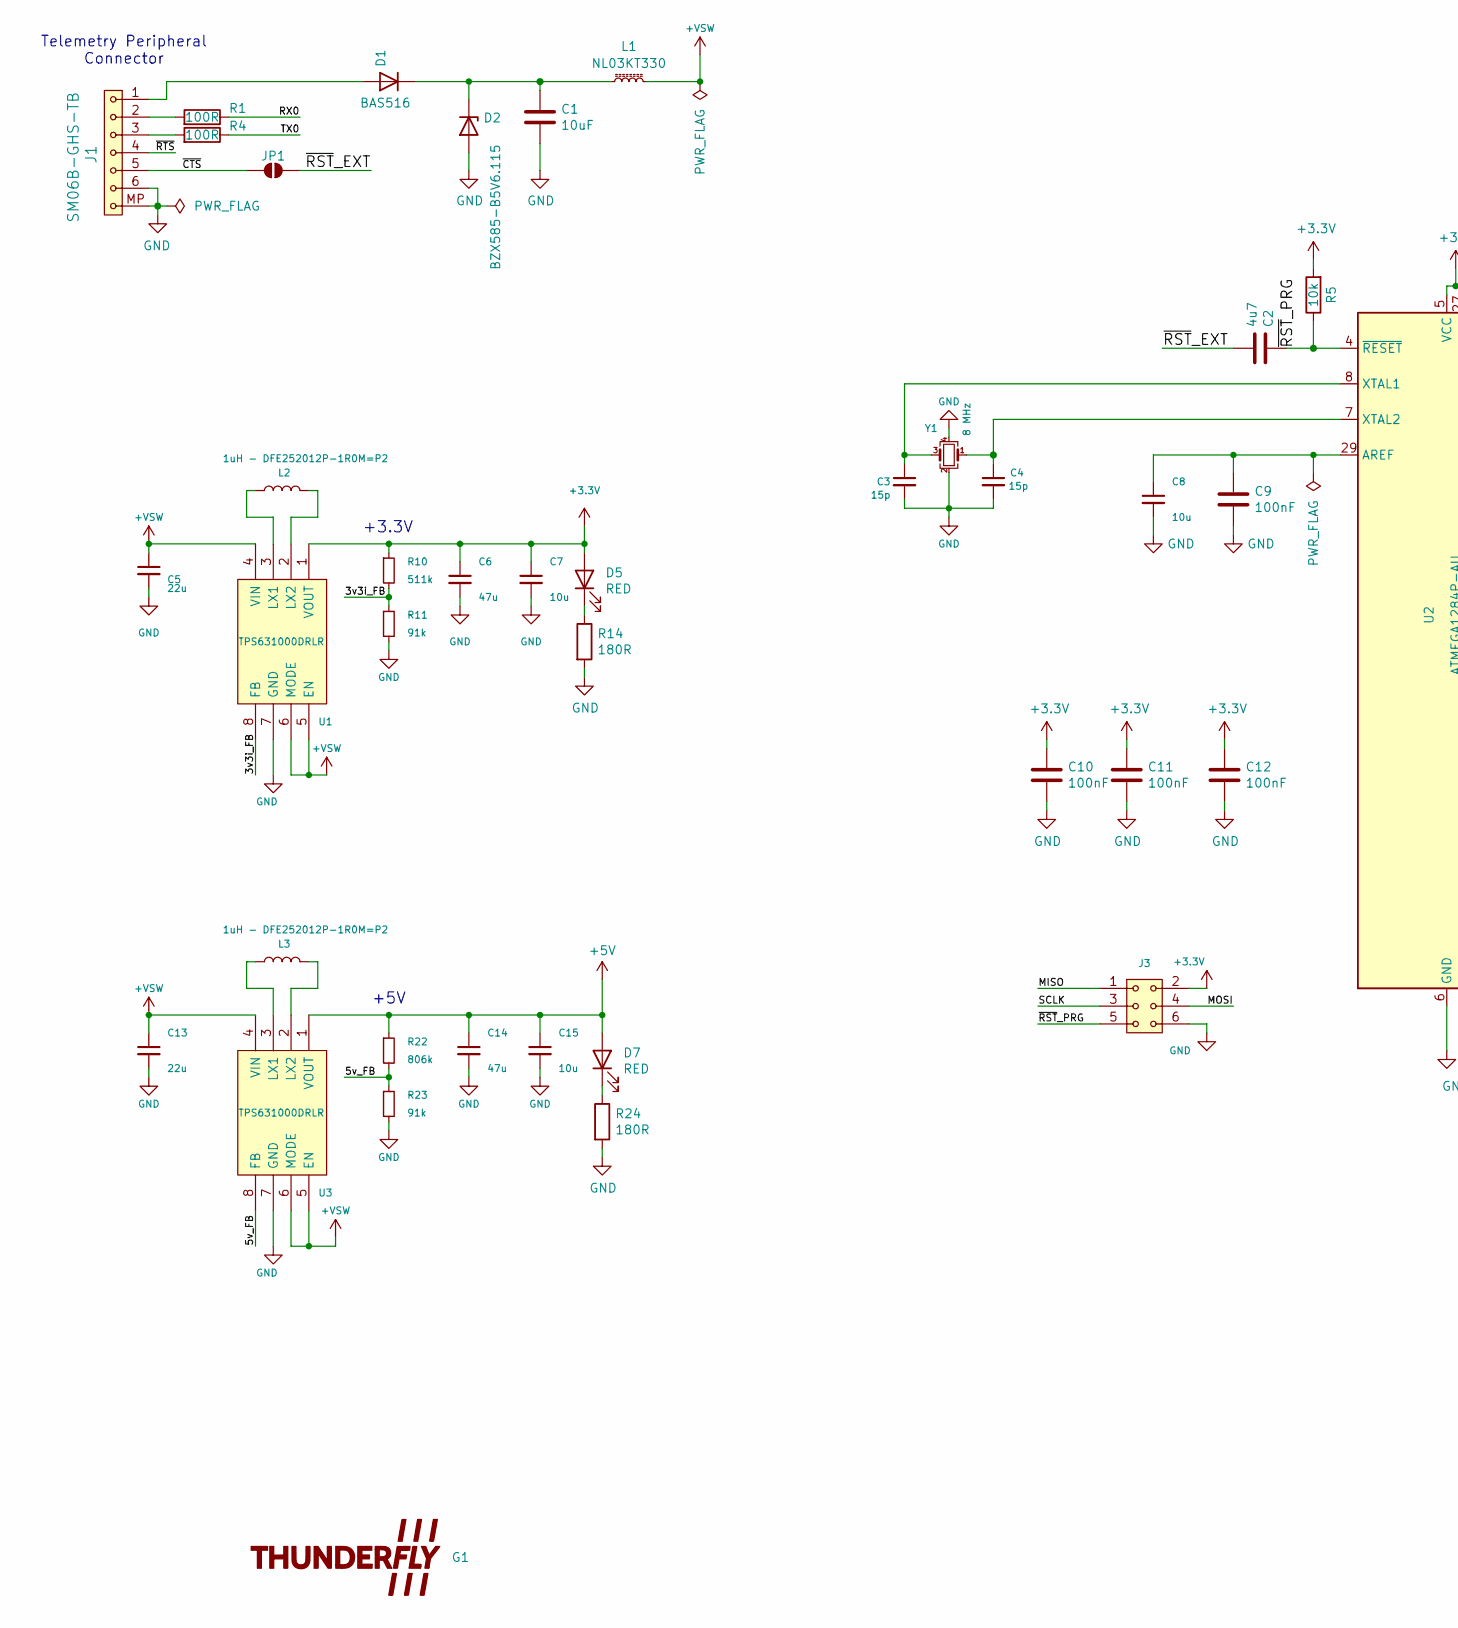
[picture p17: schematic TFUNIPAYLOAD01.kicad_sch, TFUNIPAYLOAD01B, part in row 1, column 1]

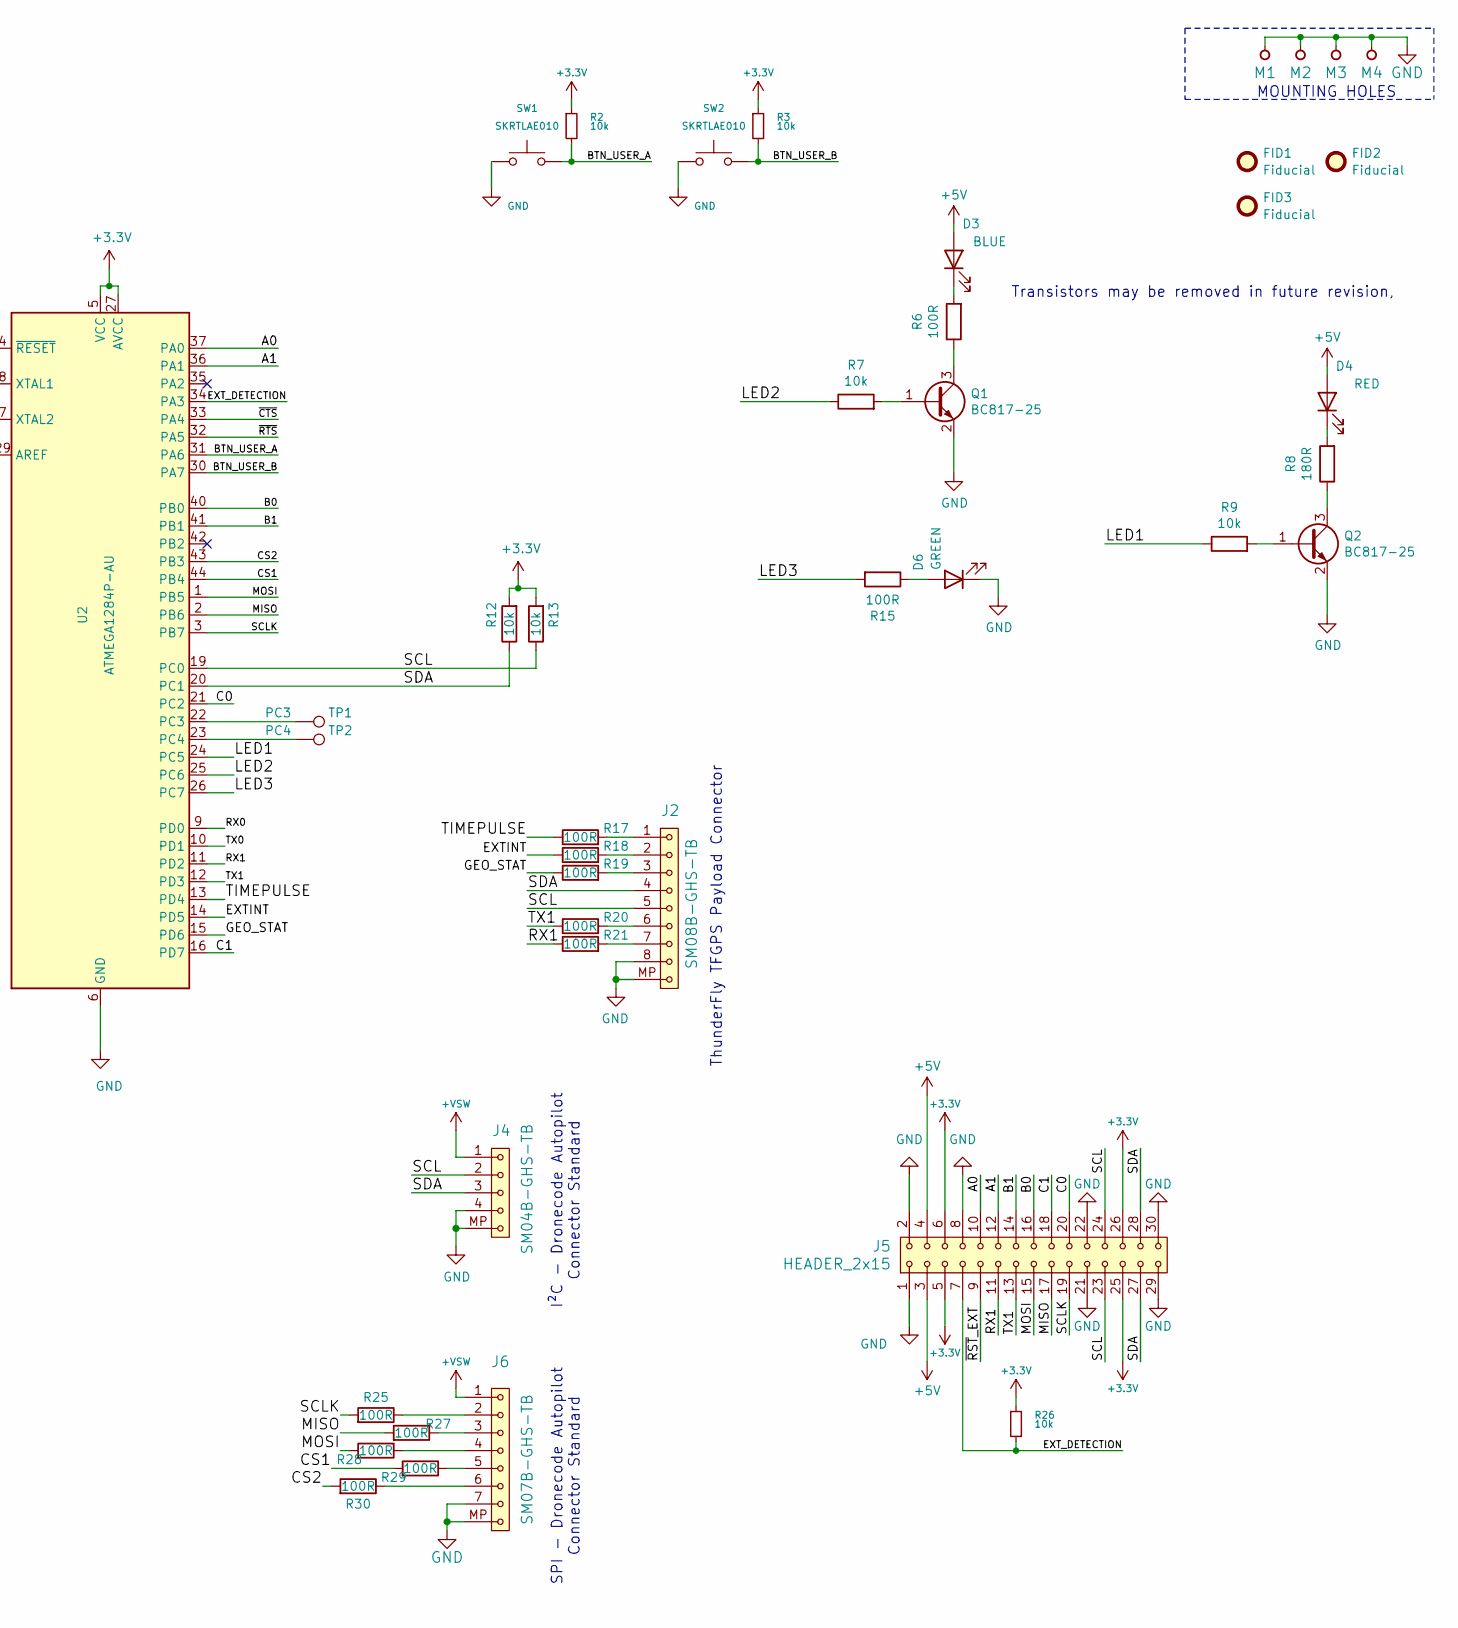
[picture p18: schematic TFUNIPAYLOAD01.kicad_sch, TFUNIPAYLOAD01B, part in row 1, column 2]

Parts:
C1: 10uF; C_0805_2012Metric
C2: 4u7; C_0805_2012Metric
C3, C4: 15p; C_0805_2012Metric
C5, C13: 22u; C_0805_2012Metric
C6, C14: 47u; C_0805_2012Metric
C7, C8, C15: 10u; C_0805_2012Metric
C9, C10, C11, C12: 100nF; C_0805_2012Metric
D1: BAS516; D_SOD-523
D2: BZX585-B5V6.115; D_SOD-523
D3: BLUE; LED_1206_mill
D4, D5, D7: RED; LED_1206_mill
D6: GREEN; LED_1206_mill
FID1, FID2, FID3: Fiducial; Fiducial_1mm_Mask2mm
G1: LOGO; TF
J1: SM06B-GHS-TB; JST_GH_SM06B-GHS-TB_1x06-1MP_P1.25mm_Horizontal
J2: SM08B-GHS-TB; JST_GH_SM08B-GHS-TB_1x08-1MP_P1.25mm_Horizontal
J3: HEADER_2x03; SMD_2x03_WO_paste
J4: SM04B-GHS-TB; JST_GH_SM04B-GHS-TB_1x04-1MP_P1.25mm_Horizontal
J5: HEADER_2x15; Straight_2x15
J6: SM07B-GHS-TB; JST_GH_SM07B-GHS-TB_1x07-1MP_P1.25mm_Horizontal
JP1: SolderJumper_2_Open; SolderJumper-2_P1.3mm_Open_RoundedPad1.0x1.5mm
L1: NL03KT330; L_0603_1608Metric_Pad1.05x0.95mm_HandSolder
L2, L3: 1uH - DFE252012P-1R0M=P2; L_1008_2520Metric
M1, M2, M3, M4: HOLE; MountingHole_3mm
Q1, Q2: BC817-25; SOT-23
R1, R4, R6, R15, R17, R18, R19, R20, R21, R25, R27, R28, R29, R30: 100R; R_0805_2012Metric
R2, R3, R5, R7, R9, R12, R13, R26: 10k; R_0805_2012Metric
R8, R14, R24: 180R; R_0805_2012Metric
R10: 511k; R_0805_2012Metric
R11, R23: 91k; R_0805_2012Metric
R22: 806k; R_0805_2012Metric
SW1, SW2: SKRTLAE010; KMT031 NGJ LHS C&K
TP1: PC3; TestPoint_Pad_D1.0mm
TP2: PC4; TestPoint_Pad_D1.0mm
U1, U3: TPS631000DRLR; SOT-583-8; Mouser Part Number 595-TPS631000DRLR
U2: ATMEGA1284P-AU; TQFP-44_10x10mm_P0.8mm
Y1: 8 MHz; Crystal_SMD_3225-4Pin_3.2x2.5mm

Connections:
+3.3V: C6.1, C7.1, C10.1, C11.1, C12.1, D5.2 (A), J3.2, J5.5, J5.6, J5.25, J5.26, R2.1, R3.1, R5.2, R10.1, R12.2, R13.2, R26.1, U1.1 (VOUT), U2.5 (VCC), U2.17 (VCC), U2.27 (AVCC), U2.38 (VCC)
+5V: C14.1, C15.1, D3.2 (A), D4.2 (A), D7.2 (A), J5.3, J5.4, R22.1, U3.1 (VOUT)
+VSW: C5.1, C13.1, J4.1, J6.1, L1.2, U1.4 (VIN), U1.5 (EN), U1.6 (MODE), U3.4 (VIN), U3.5 (EN), U3.6 (MODE)
/3v3i_FB: R10.2, R11.1, U1.8 (FB)
/5v_FB: R22.2, R23.1, U3.8 (FB)
/A0: J5.10, U2.37 (PA0)
/A1: J5.12, U2.36 (PA1)
/B0: J5.16, U2.40 (PB0)
/B1: J5.14, U2.41 (PB1)
/BTN_USER_A: R2.2, SW1.1, U2.31 (PA6)
/BTN_USER_B: R3.2, SW2.1, U2.30 (PA7)
/C0: J5.20, U2.21 (PC2)
/C1: J5.18, U2.16 (PD7)
/CS1: R29.2, U2.44 (PB4)
/CS2: R30.2, U2.43 (PB3)
/EXTINT: R18.1, U2.14 (PD5)
/EXT_DETECTION: J5.7, R26.2, U2.34 (PA3)
/GEO_STAT: R19.1, U2.15 (PD6)
/LED1: R9.1, U2.24 (PC5)
/LED2: R7.1, U2.25 (PC6)
/LED3: R15.2, U2.26 (PC7)
/MISO: J3.1, J5.17, R27.2, U2.2 (PB6)
/MOSI: J3.4, J5.15, R28.2, U2.1 (PB5)
/RX0: R1.1, U2.9 (PD0)
/RX1: J5.11, R21.1, U2.11 (PD2)
/SCL: J2.5, J4.2, J5.23, J5.24, R13.1, U2.19 (PC0)
/SCLK: J3.3, J5.19, R25.2, U2.3 (PB7)
/SDA: J2.4, J4.3, J5.27, J5.28, R12.1, U2.20 (PC1)
/TIMEPULSE: R17.1, U2.13 (PD4)
/TX0: R4.1, U2.10 (PD1)
/TX1: J5.13, R20.1, U2.12 (PD3)
/~CTS: J1.5, JP1.2 (B), U2.33 (PA4)
/~RST_EXT: C2.2, J5.9, JP1.1 (A)
/~RST_PRG: C2.1, J3.5, R5.1, U2.4 (~RESET)
/~RTS: J1.4, U2.32 (PA5)
GND: C1.2, C3.2, C4.2, C5.2, C6.2, C7.2, C8.2, C9.2, C10.2, C11.2, C12.2, C13.2, C14.2, C15.2, D2.2 (A), D6.1 (K), J1.6, J1.MP, J2.8, J2.MP, J3.6, J4.4, J4.MP, J5.1, J5.2, J5.8, J5.21, J5.22, J5.29, J5.30, J6.7, J6.MP, M1.1, M2.1, M3.1, M4.1, Q1.2 (E), Q2.2 (E), R11.2, R14.2, R23.2, R24.2, SW1.2, SW2.2, U1.7 (GND), U2.6 (GND), U2.18 (GND), U2.28 (GND), U2.39 (GND), U3.7 (GND), Y1.2, Y1.4
unnamed: D1.2 (A), J1.1
unnamed: C1.1, D1.1 (K), D2.1 (K), L1.1
unnamed: D3.1 (K), R6.2
unnamed: D4.1 (K), R8.2
unnamed: D5.1 (K), R14.1
unnamed: D6.2 (A), R15.1
unnamed: D7.1 (K), R24.1
unnamed: J1.2, R1.2
unnamed: J1.3, R4.2
unnamed: J2.1, R17.2
unnamed: J2.2, R18.2
unnamed: J2.3, R19.2
unnamed: J2.6, R20.2
unnamed: J2.7, R21.2
unnamed: J6.2, R25.1
unnamed: J6.3, R27.1
unnamed: J6.4, R28.1
unnamed: J6.5, R29.1
unnamed: J6.6, R30.1
unnamed: Q1.1 (B), R7.2
unnamed: Q1.3 (C), R6.1
unnamed: Q2.1 (B), R9.2
unnamed: Q2.3 (C), R8.1
unnamed: L2.1, U1.3 (LX1)
unnamed: L2.2, U1.2 (LX2)
unnamed: C8.1, C9.1, U2.29 (AREF)
unnamed: TP1.1, U2.22 (PC3)
unnamed: TP2.1, U2.23 (PC4)
unnamed: C3.1, U2.8 (XTAL1), Y1.3
unnamed: C4.1, U2.7 (XTAL2), Y1.1
unnamed: L3.1, U3.3 (LX1)
unnamed: L3.2, U3.2 (LX2)

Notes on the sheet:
I²C - Dronecode Autopilot Connector Standard
Transistors may be removed in future revision,
SPI - Dronecode Autopilot Connector Standard
ThunderFly TFGPS Payload Connector
Telemetry Peripheral Connector
+5V
+3.3V
MOUNTING HOLES

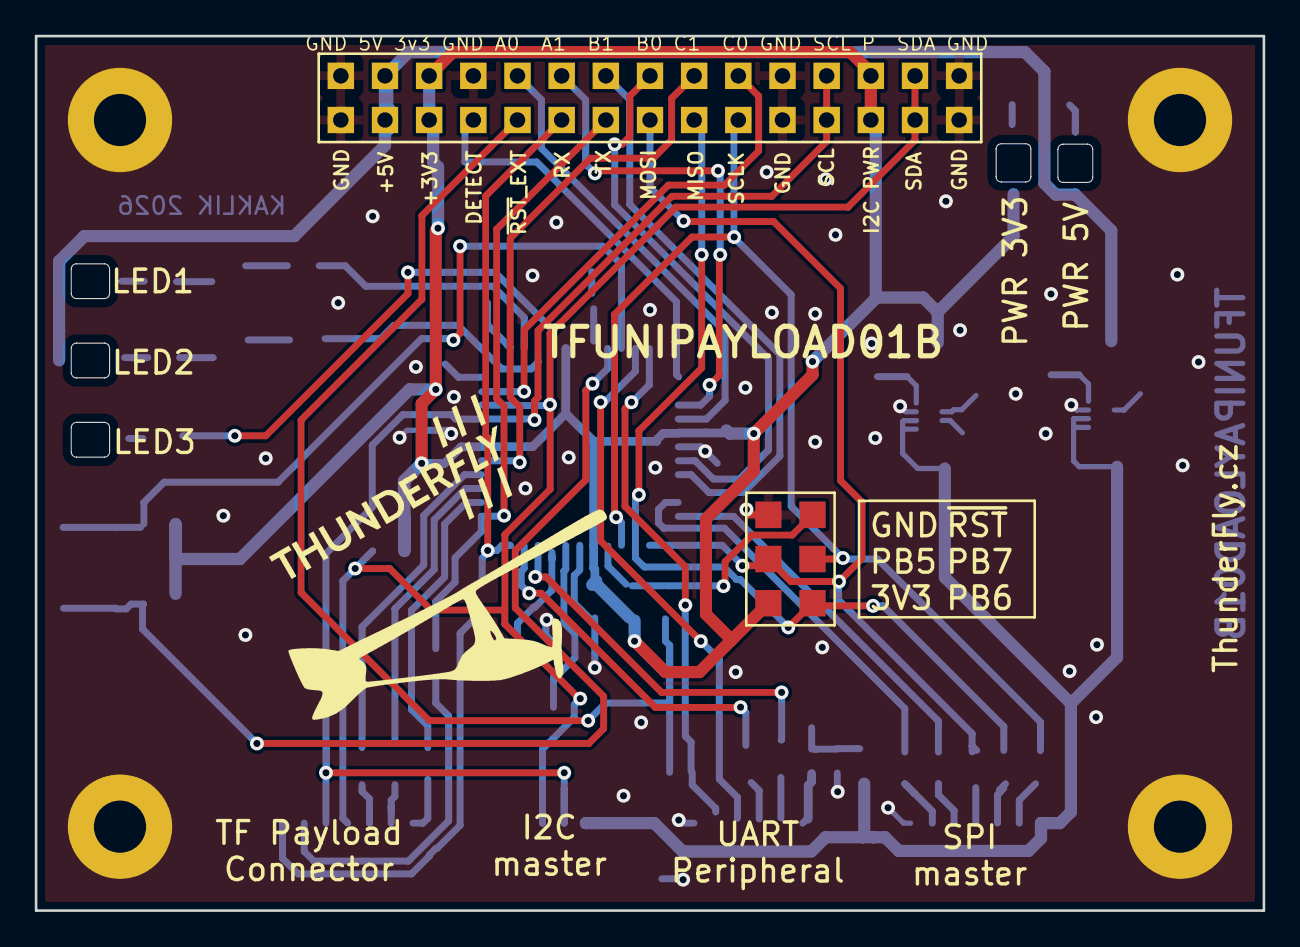
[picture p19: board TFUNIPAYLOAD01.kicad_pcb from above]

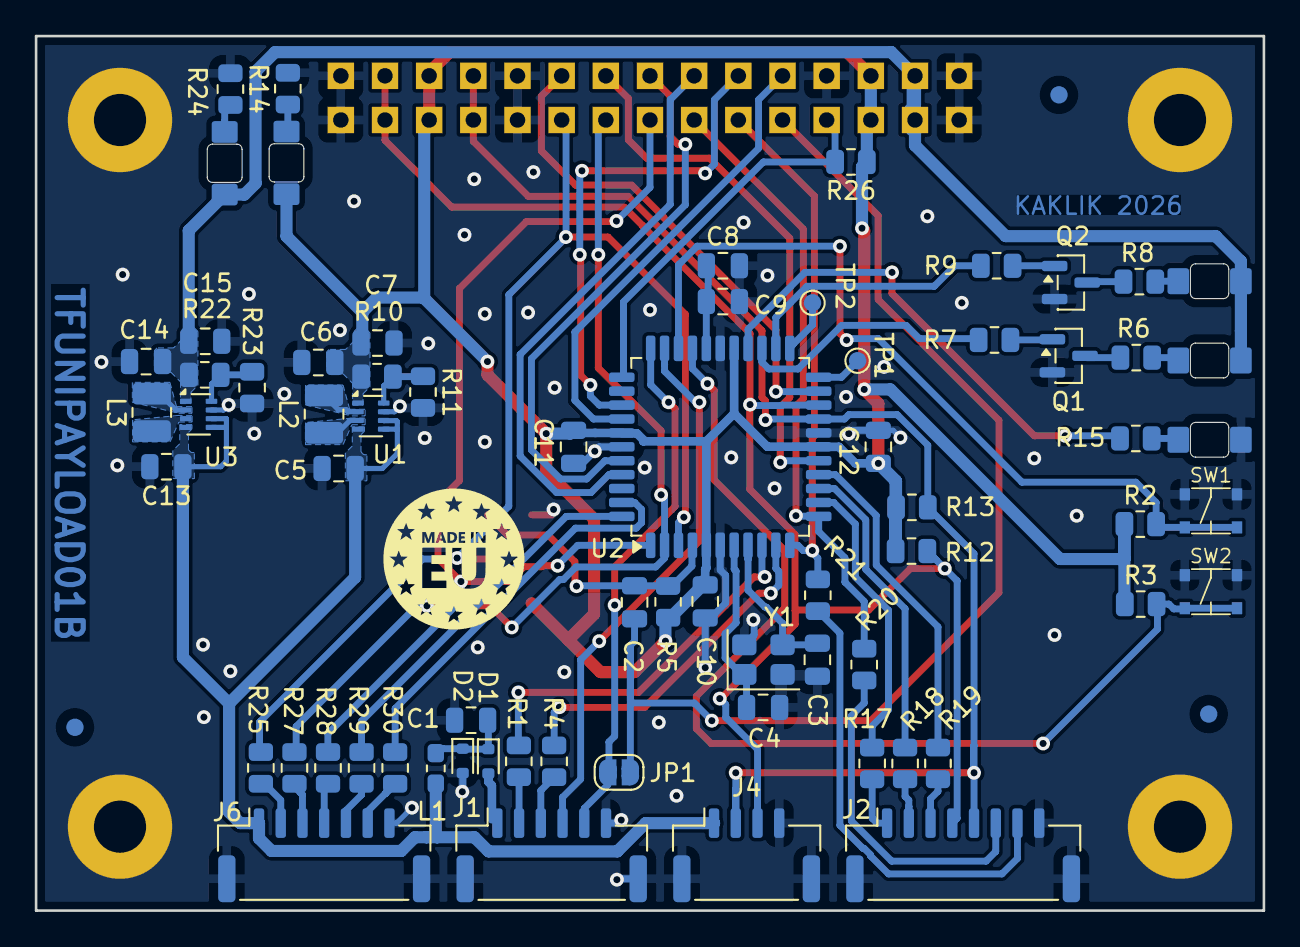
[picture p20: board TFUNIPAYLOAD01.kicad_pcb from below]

Board: 2 copper layers, 70.6 x 50.3 mm, 79 parts (72 on the bottom side), 68 nets.

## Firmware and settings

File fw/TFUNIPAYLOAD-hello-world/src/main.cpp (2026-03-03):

/*
  TFUNIPAYLOAD01B
  ATmega1284P @ 8 MHz (external oscillator)

                     Mighty 1284p
                      +---\/---+
           (D 0) PB0 1|        |40 PA0 (AI 0 / D24)
           (D 1) PB1 2|        |39 PA1 (AI 1 / D25)
      INT2 (D 2) PB2 3|        |38 PA2 (AI 2 / D26)
       PWM (D 3) PB3 4|        |37 PA3 (AI 3 / D27)
    PWM/SS (D 4) PB4 5|        |36 PA4 (AI 4 / D28)
      MOSI (D 5) PB5 6|        |35 PA5 (AI 5 / D29)
  PWM/MISO (D 6) PB6 7|        |34 PA6 (AI 6 / D30)
   PWM/SCK (D 7) PB7 8|        |33 PA7 (AI 7 / D31)
                 RST 9|        |32 AREF
                VCC 10|        |31 GND
                GND 11|        |30 AVCC
              XTAL2 12|        |29 PC7 (D 23)
              XTAL1 13|        |28 PC6 (D 22)
      RX0 (D 8) PD0 14|        |27 PC5 (D 21) TDI
      TX0 (D 9) PD1 15|        |26 PC4 (D 20) TDO
RX1/INT0 (D 10) PD2 16|        |25 PC3 (D 19) TMS
TX1/INT1 (D 11) PD3 17|        |24 PC2 (D 18) TCK
     PWM (D 12) PD4 18|        |23 PC1 (D 17) SDA
     PWM (D 13) PD5 19|        |22 PC0 (D 16) SCL
     PWM (D 14) PD6 20|        |21 PD7 (D 15) PWM
                      +--------+
*/

#include <Arduino.h>

#if !defined(PIN_LED_RED) || !defined(PIN_LED_BLUE) || !defined(PIN_LED_GREEN) || !defined(PIN_BTN_USER_A) || !defined(PIN_BTN_USER_B)
#error "Board macros PIN_LED_* and PIN_BTN_USER_* must be provided by board configuration"
#endif

static bool phase = false;
static uint32_t counter = 0;
static uint32_t lastBlinkToggleMs = 0;

void setup()
{
  Serial.begin(115200);

  pinMode(PIN_LED_RED, OUTPUT);
  pinMode(PIN_LED_BLUE, OUTPUT);
  pinMode(PIN_LED_GREEN, OUTPUT);

  // Buttons have external pull-up resistors and are active in LOW state.
  pinMode(PIN_BTN_USER_A, INPUT);
  pinMode(PIN_BTN_USER_B, INPUT);

  digitalWrite(PIN_LED_GREEN, LOW);
  digitalWrite(PIN_LED_BLUE, HIGH);
  digitalWrite(PIN_LED_RED, HIGH);

  lastBlinkToggleMs = millis();

  Serial.println("TFUNIPAYLOAD01 hello-world");
}

void loop()
{
  const bool btnAIsPressed = digitalRead(PIN_BTN_USER_A) == LOW;
  const bool btnBIsPressed = digitalRead(PIN_BTN_USER_B) == LOW;

  uint16_t blinkDelayMs = 500;
  if (btnAIsPressed && btnBIsPressed) {
    blinkDelayMs = 80;
  } else if (btnAIsPressed) {
    blinkDelayMs = 150;
  } else if (btnBIsPressed) {
    blinkDelayMs = 1000;
  }

  const bool anyButtonIsPressed = btnAIsPressed || btnBIsPressed;

  digitalWrite(PIN_LED_RED, anyButtonIsPressed);

  const uint32_t nowMs = millis();
  if (nowMs - lastBlinkToggleMs >= blinkDelayMs) {
    lastBlinkToggleMs = nowMs;
    phase = !phase;

    digitalWrite(PIN_LED_GREEN, phase ? HIGH : LOW);
    digitalWrite(PIN_LED_BLUE, phase ? LOW : HIGH);

    counter++;
    Serial.print("line=");
    Serial.print(counter);
    Serial.print(" uptime=");
    Serial.print(millis() / 1000UL);
    Serial.print("s btnA=");
    Serial.print(btnAIsPressed ? "pressed" : "released");
    Serial.print(" btnB=");
    Serial.print(btnBIsPressed ? "pressed" : "released");
    Serial.print(" blink=");
    Serial.print(blinkDelayMs);
    Serial.println("ms");
  }
}

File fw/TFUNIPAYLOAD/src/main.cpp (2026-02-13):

#include <Arduino.h>
#include "ArduinoMavlink.h"
#include <HardwareSerial.h>
#include "githash.h"

#define MAJOR 0
#define MINOR 1


HardwareSerial &hs = Serial1;
ArduinoMavlink mav(hs);

unsigned long current_ms;

unsigned long heartbeat_previous_time = 0;
const long heartbeat_period = 500;
unsigned long data_previous_time = 0;
const long data_period = 1000;

boolean led_status = false;
//uint8_t data[] = "Hello World!";
uint8_t data[2];

void setup() {
  Serial.begin(57600);
  while(!mav.begin()){
    Serial.println("Not Connected!");
    delay(250);
  }
  mav.Stream();
  delay(2000);
}


void loop() {

//  periodical stuff
  current_ms = millis();
  
  if( current_ms > (heartbeat_previous_time + heartbeat_period)){
    heartbeat_previous_time = current_ms;
    
    mav.SendHeartBeat();
    // mav.SendTunnelData(data, 10, 0, 1, 1);
  }
  
  if( current_ms > (data_previous_time + data_period)){
    data_previous_time = current_ms;
    
    data[0] = random(255);
    data[1] = random(255);

    // data array (max length 128), data array size, data type (0 default - unknown), target sysid, target compid
    // For unicast (only for logging purposes) set sysid and compid to match the autopilot. For realtime visualisation, you can
    // set sysid and comid to broadcast (0, 0)
    mav.SendTunnelData(data, sizeof(data), 0, 0, 0);
    
    led_status = !led_status;
    digitalWrite(13, led_status);
  }

  delay(10);
}

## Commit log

2021-02-04 Add block schematics to the readme.
2023-12-30 Update README.md
    Generic information about supported TF-ATMON sensors is moved to the https://github.com/ThunderFly-aerospace/TF-ATMON repository.
2025-11-18 Initial schematics. #2 WIP
    [TFUNIPAYLOAD01.kicad_pcb, TFUNIPAYLOAD01.kicad_sch]
2025-11-25 Update schematics. Resolve #2
    [TFUNIPAYLOAD01.kicad_pcb, TFUNIPAYLOAD01.kicad_sch]
2025-11-25 Update actions products
    [TFUNIPAYLOAD01-B_Courtyard.dxf, TFUNIPAYLOAD01-B_Cu.dxf, TFUNIPAYLOAD01-B_Fab.dxf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]
2025-11-25 Fix ERC errors. Fix #3.
    [TFUNIPAYLOAD01.kicad_pcb, TFUNIPAYLOAD01.kicad_sch]
2025-12-27 PCB layout WIP.
    [TFUNIPAYLOAD01.kicad_pcb, TFUNIPAYLOAD01.kicad_sch]
2025-12-27 Components placement.
    [TFUNIPAYLOAD01.kicad_pcb, TFUNIPAYLOAD01.kicad_sch]
2025-12-27 Footprints updated.
    [TFUNIPAYLOAD01.kicad_pcb, TFUNIPAYLOAD01.kicad_sch]
2025-12-27 Pinheader correctly positioned.
    [TFUNIPAYLOAD01.kicad_pcb, TFUNIPAYLOAD01.kicad_sch]
2025-12-28 Pinheader changed to footprint with square pads. Routing more nets.
    [TFUNIPAYLOAD01.kicad_pcb, TFUNIPAYLOAD01.kicad_sch]
2025-12-28 Routed PCB.
    [TFUNIPAYLOAD01.kicad_pcb, TFUNIPAYLOAD01.kicad_sch]
2025-12-29 Improve layout.
    [TFUNIPAYLOAD01.kicad_pcb, TFUNIPAYLOAD01.kicad_sch]
2026-01-07 Improve layout and graphics.
    [TFUNIPAYLOAD01.kicad_pcb]
2026-01-09 Improve silkscreen.
    [TFUNIPAYLOAD01.kicad_pcb]
2026-01-20 Improve connector description.
    [TFUNIPAYLOAD01.kicad_pcb, TFUNIPAYLOAD01.kicad_sch]
2026-01-21 Create dimensioned drawings.
    [TFUNIPAYLOAD01.kicad_pcb]
2026-01-25 Adding Made in EU symbol.
    [TFUNIPAYLOAD01.kicad_pcb]
2026-02-13 move current arduino fw into platformIO projects
2026-02-13 Update build_fw.yml
    create build directory in SW/arduino/
2026-02-14 Delete SW/arduino directory
    Sources moved to fw directory as platformIO projects.
2026-02-15 Automatic update of KiCAD outputs
    [TFUNIPAYLOAD01.step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]
2026-02-16 Unify PlatformIO board definition across firmware projects (#13)
    Make PlatformIO board configuration shared across project directories.
2026-02-16 Unify PlatformIO board definition across firmware projects (#13), extended build
2026-02-16 Add definition of buttons and LEDs.
2026-02-16 Add definition of buttons and LEDs., extended build
2026-02-17 Add LED blinking.
2026-02-17 Add LED blinking., extended build
2026-02-17 Configure bootloader LED.
2026-02-17 Configure bootloader LED., extended build
2026-03-02 Fix LED resistors values.
    [TFUNIPAYLOAD01.kicad_pcb, TFUNIPAYLOAD01.kicad_sch]
2026-03-03 Fix red LED swith on in case any button pressed.
    [main.cpp]
2026-03-03 Fix red LED swith on in case any button pressed., extended build
